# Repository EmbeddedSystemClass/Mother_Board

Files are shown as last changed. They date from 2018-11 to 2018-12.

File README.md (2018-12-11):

# ZJUNlict Mother Board Description
 
The mother board is used to convert between different logic levels (5V TTL <-> 3.3V TTL), improve signal quality and provide interface to the [motor driver board](https://github.com/ZJUNlict/Motor_Driver_Board), the [core board](https://github.com/ZJUNlict/Core_Board), the [nRF2401A](https://www.nordicsemi.com/eng/Products/2.4GHz-RF/nRF2401A) module, four [encoders](https://www.usdigital.com/) and a infrared sensor. (The board is designed using [Altium Designer](https://www.altium.com/altium-designer/) 17.1)

The 2D and 3D design views are shown below:

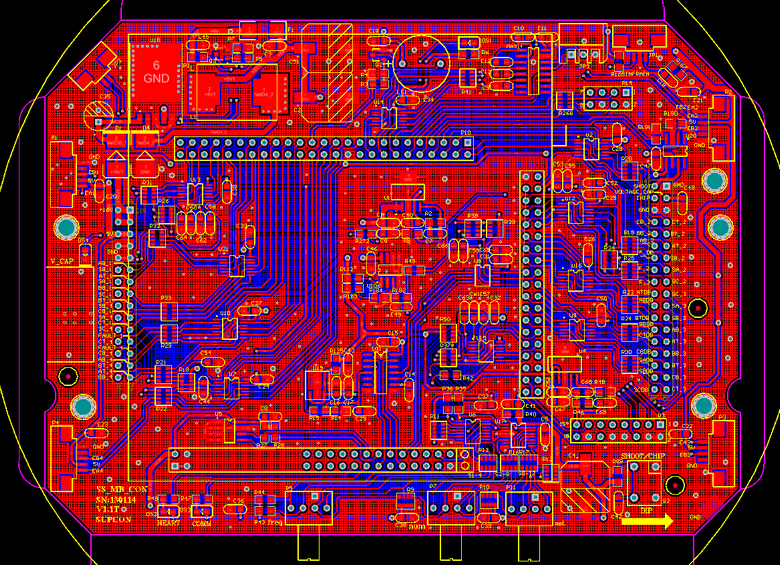
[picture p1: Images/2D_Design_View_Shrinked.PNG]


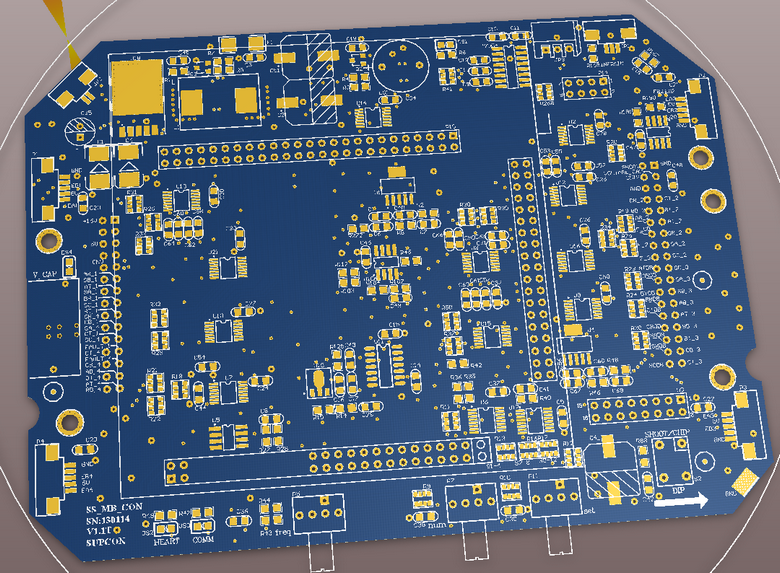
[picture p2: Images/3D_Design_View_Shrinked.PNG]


The main features are:

* Provide power supply (LM2576T-5.0 and TPS79401) for the core board and components on the mother board. (LiPo Battery (4S) 14.8-16.8V to 5V and 3.3V)
* Schmitt-trigger inverters (74LV14A, SN74HC14) complete the logic level convert and improve the signal quality.
* A/D (TLC0834) measures the battery and capacitor voltage.
* I/O expander (PCA9557PW) and rotary DIP switch (A6R/A6RV) for easier robot number, frequency and mode set.
* EEPROM (AT24C08) stores calibration data for each robot.
* Serial port (MAX232CSE) for communication with PC.

The photos of the mother board are shown below as references. 

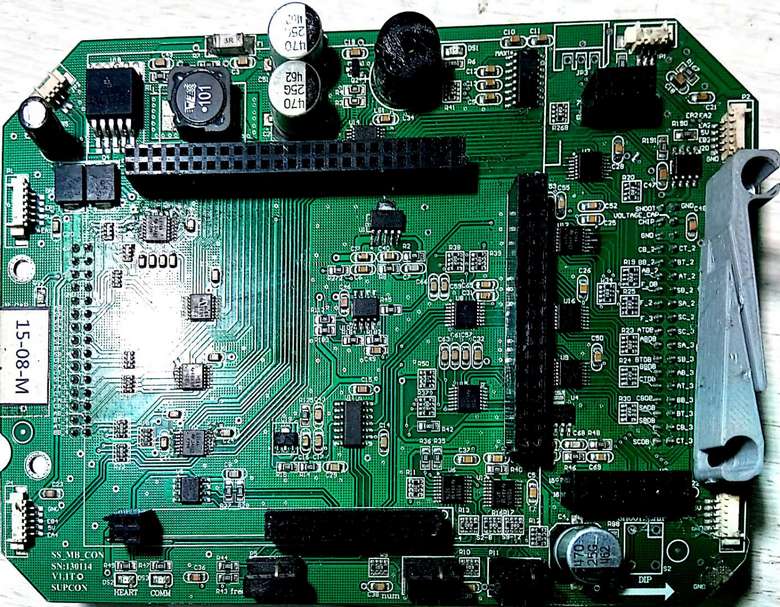
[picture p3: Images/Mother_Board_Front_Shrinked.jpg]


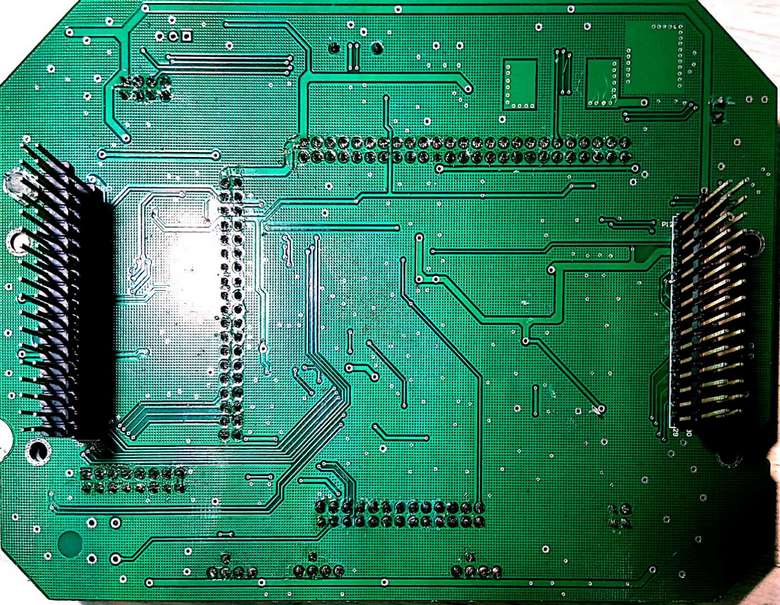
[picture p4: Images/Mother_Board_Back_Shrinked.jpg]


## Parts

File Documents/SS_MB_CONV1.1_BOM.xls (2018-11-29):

No. | Name | Code | Spec | Pos | Brand | Package | Quantity | Unit | Attribute | Notice
110021001 | IC | AT24C08B-SH |  | U5 | Atmel | SO-G8 | 1
110031001 | IC | LM393D |  | U106 |  | SOIC-8 | 1
110031003 | IC | 74HC14PW |  | U2, U9, U10, U16, U21 |  | TSSOP14 | 5
110031004 | IC | 74LVC14APW |  | U7, U8, U12, U13, U14, U15, |  | TSSOP14 | 6
110031005 | IC | PCA9557PW |  | U6, U17 |  | TSSOP16 | 2
110051001 | MAX232CSE(16) |  | +-15KV ESD-PROTECTED, +5V RS-232 TRANSCEIVERS | MAX1 |  | NSO16 | 1
110051004 | IC | TLC0834CD |  | U11 |  | SO-14 | 1
110051005 | IC | MC34152DG |  | U20 |  | SOIC-8 | 1
110061001 | IC | TPS79401/501 |  | U1, U4 |  | SOT223-6 | 2
110061002 | IC | LM2576D2T-005G |  | U18 |  | D2PAK | 1
111011001 | LED |  | 1.7V,0805,Green | DS1, DS2，DS3, DS4 |  | 0805D | 4
112011001 | Diode |  | SS36，60V,3A | D1, D4 |  | DO-214AB | 2
112021001 | Triode | 9014B |  | Q2, Q3 |  | SO-G3/Y1 | 2
112031001 | Voltage Reference | TL431ACPK |  | U19 | TI | SOT89 | 1
113021001 | Inductance | MSS1260T-100uH |  | L1 | Coilcraft | L | 1
115021001 | Resistance |  | 2.2K 1% | R3, R5 |  | 0805R | 2
115021002 | Resistance |  | 300 1% | R1 |  | 0805R | 1
115021003 | Resistance |  | 51k 1% | R2, R46 |  | 0805R | 2
115021005 | Resistance |  | 1.6K1% | R35, R36 |  | 0805R | 2
115021007 | Resistance |  | 100 1% | R167 |  | 0805R | 1
115021008 | Resistance |  | 10k 1% | R27, R28, R43, R44, R45, R88, R182, R183, R190, R191 |  | 0805R | 10
115021010 | Resistance |  | 1K 1% | R4, R7, R40, R112, R272 |  | 0805R | 5
115021013 | Resistance |  | 20K 1% | R168 |  | 0805R | 1
115021014 | Resistance |  | 22 1% | R42 |  | 0805R | 1
115021015 | Resistance |  | 22k1% | R15 |  | 0805R | 1
115021016 | Resistance |  | 2K 1% | R184 |  | 0805R | 1
115021017 | Resistance |  | 3.3k 1% | R14 |  | 0805R | 1
115011009 | Resistance |  | 30k 1% | R8, R48 |  | 0805R | 2
115021022 | Resistance |  | 470 1% | R125 |  | 0805R | 1
115021024 | Resistance |  | 510 1% | R6, R47, R49 |  | 0805R | 3
115051001 | Resisters Packs |  | 10K 1% | R9, R10, R12, R18, R26, R34, R39 |  | 0603 Resisters Packs | 7
115051002 | Resisters Packs |  | 2K 1% | R11,R50 |  | 0603 Resisters Packs | 2
115051003 | Resisters Packs |  | 22 1% | R13, R16, R17, R19, R20, R21, R22, R23, R24, R25, R29, R30, R31, R32, R33, R37, R38, R41, R268 |  | 0603 Resisters Packs | 19
115101001 | Fuse | 504-TR1/6125TD3-R | 3A 60V Slow Blow 2410 | F1 |  | 2512r | 1
116010002 | Electrolytic Capacitor | CAPPR2.5-6.3，6.3*11， | 100uf，25V,-55to+105℃ | C35 |  |  | 1
116011001 | Electrolytic Capacitor | J10 | 25V 470uf 10*10,-55to+105℃ | C2, C4, C51 | NICHICON |  | 3
116051001 | Ceramic Capacitor | 805 | 0.01uf,±10%，50V，-55to+125℃ | C44, C52, C53, C54, C55, C57, C58,C59, C60, C61, C62, C63, C64, C65, C66 |  |  | 15
116051002 | Ceramic Capacitor |  | 0.1uf,±10%，50V， -55to+125℃ | C3, C5, C6, C8, C14, C15, C17, C19, C20, C21, C22, C23, C24, C25, C26, C27, C28, C29, C30, C31, C32, C33, C34, C36, C37, C38, C39, C41, C42, C43, C45, C46, C47, C48, C49, C50, C67 |  | 805 | 37
116051005 | Ceramic Capacitor |  | 15pf,±10%，50V， -55to+125℃ | C7, C68 |  | 805 | 2
116051008 | Ceramic Capacitor |  | 1uf,±10%，50V， -55to+125℃ | C1, C9, C10, C11, C12, C13, C16, C56 |  | 805 | 8
116051009 | Ceramic Capacitor |  | 2.2uf,±10%，50V， -55to+125℃ | C40, C69 |  | 805 | 2
116051011 | Ceramic Capacitor |  | 4.7uf,±10%，50V， -55to+125℃ | C18 |  | 805 | 1
117020001 | Button | CTS-61R-V |  | S2 | CHAU-HUA |  | 1
117040001 | Rotary DIP Switch | A6RV-161RF |  | P5, P7, P11 | CHAU-HUA | A6RV-161RS | 3
118031001 | Connector | 1132R-SMT-3P |  | JP1 | SHPEAK | SMD-3P-1.25 | 1
118031002 | Connector | 1132R-SMT-2P |  | JP2 | SHPEAK | SMD-2P-1.25 | 1
118031003 | Connector | 1132R-SMT-5P |  | P1, P2, P3, P4 | SHPEAK | SMD-5P-1.25 | 4
118040001 | Connector | 201DLS-2*18PG-8.5/13.8/3.0 |  | P13 | SHPEAK | HDR2X18 | 1
118040002 | Connector | 203S-3C-2X4P-8.5/3.0 |  | P14 | SHPEAK | HDR2X4 | 1
118050004 | nRF2401A Connector | 203S-3C-2X8P-8.5/3.0 |  | U3 | SHPEAK | HDR2X8 | 1
118050002 | Connector | 203S-3C-2X25P-8.5/3.0 |  | 1 | SHPEAK |  | 1
118050022 | Connector | 203S-3C-2X19P-8.5/3.0 |  | 1 | SHPEAK |  | 1
118050036 | Connector | 203S-3C-2X13P-8.5/3.0 |  | 1 | SHPEAK |  | 1
118050037 | Connector | 203S-3C-2X2P-8.5/3.0 |  | 1 | SHPEAK |  | 1
118050006 | Connector | 201DLS-2*15PG-8.5/13.8/3.0 |  | P12 | SHPEAK | HDR2X15 | 1
119020001 | Buzzer | SD1209T5-A1 | 5V 60mA 12mm*9mm | LS1 | TDK | Buzzer | 1
133010001 | nRF Module | NRF2401A |  |  |  |  | 1
135010001 | Core Board | EP3C25 |  |  | ALTERA |  | 1

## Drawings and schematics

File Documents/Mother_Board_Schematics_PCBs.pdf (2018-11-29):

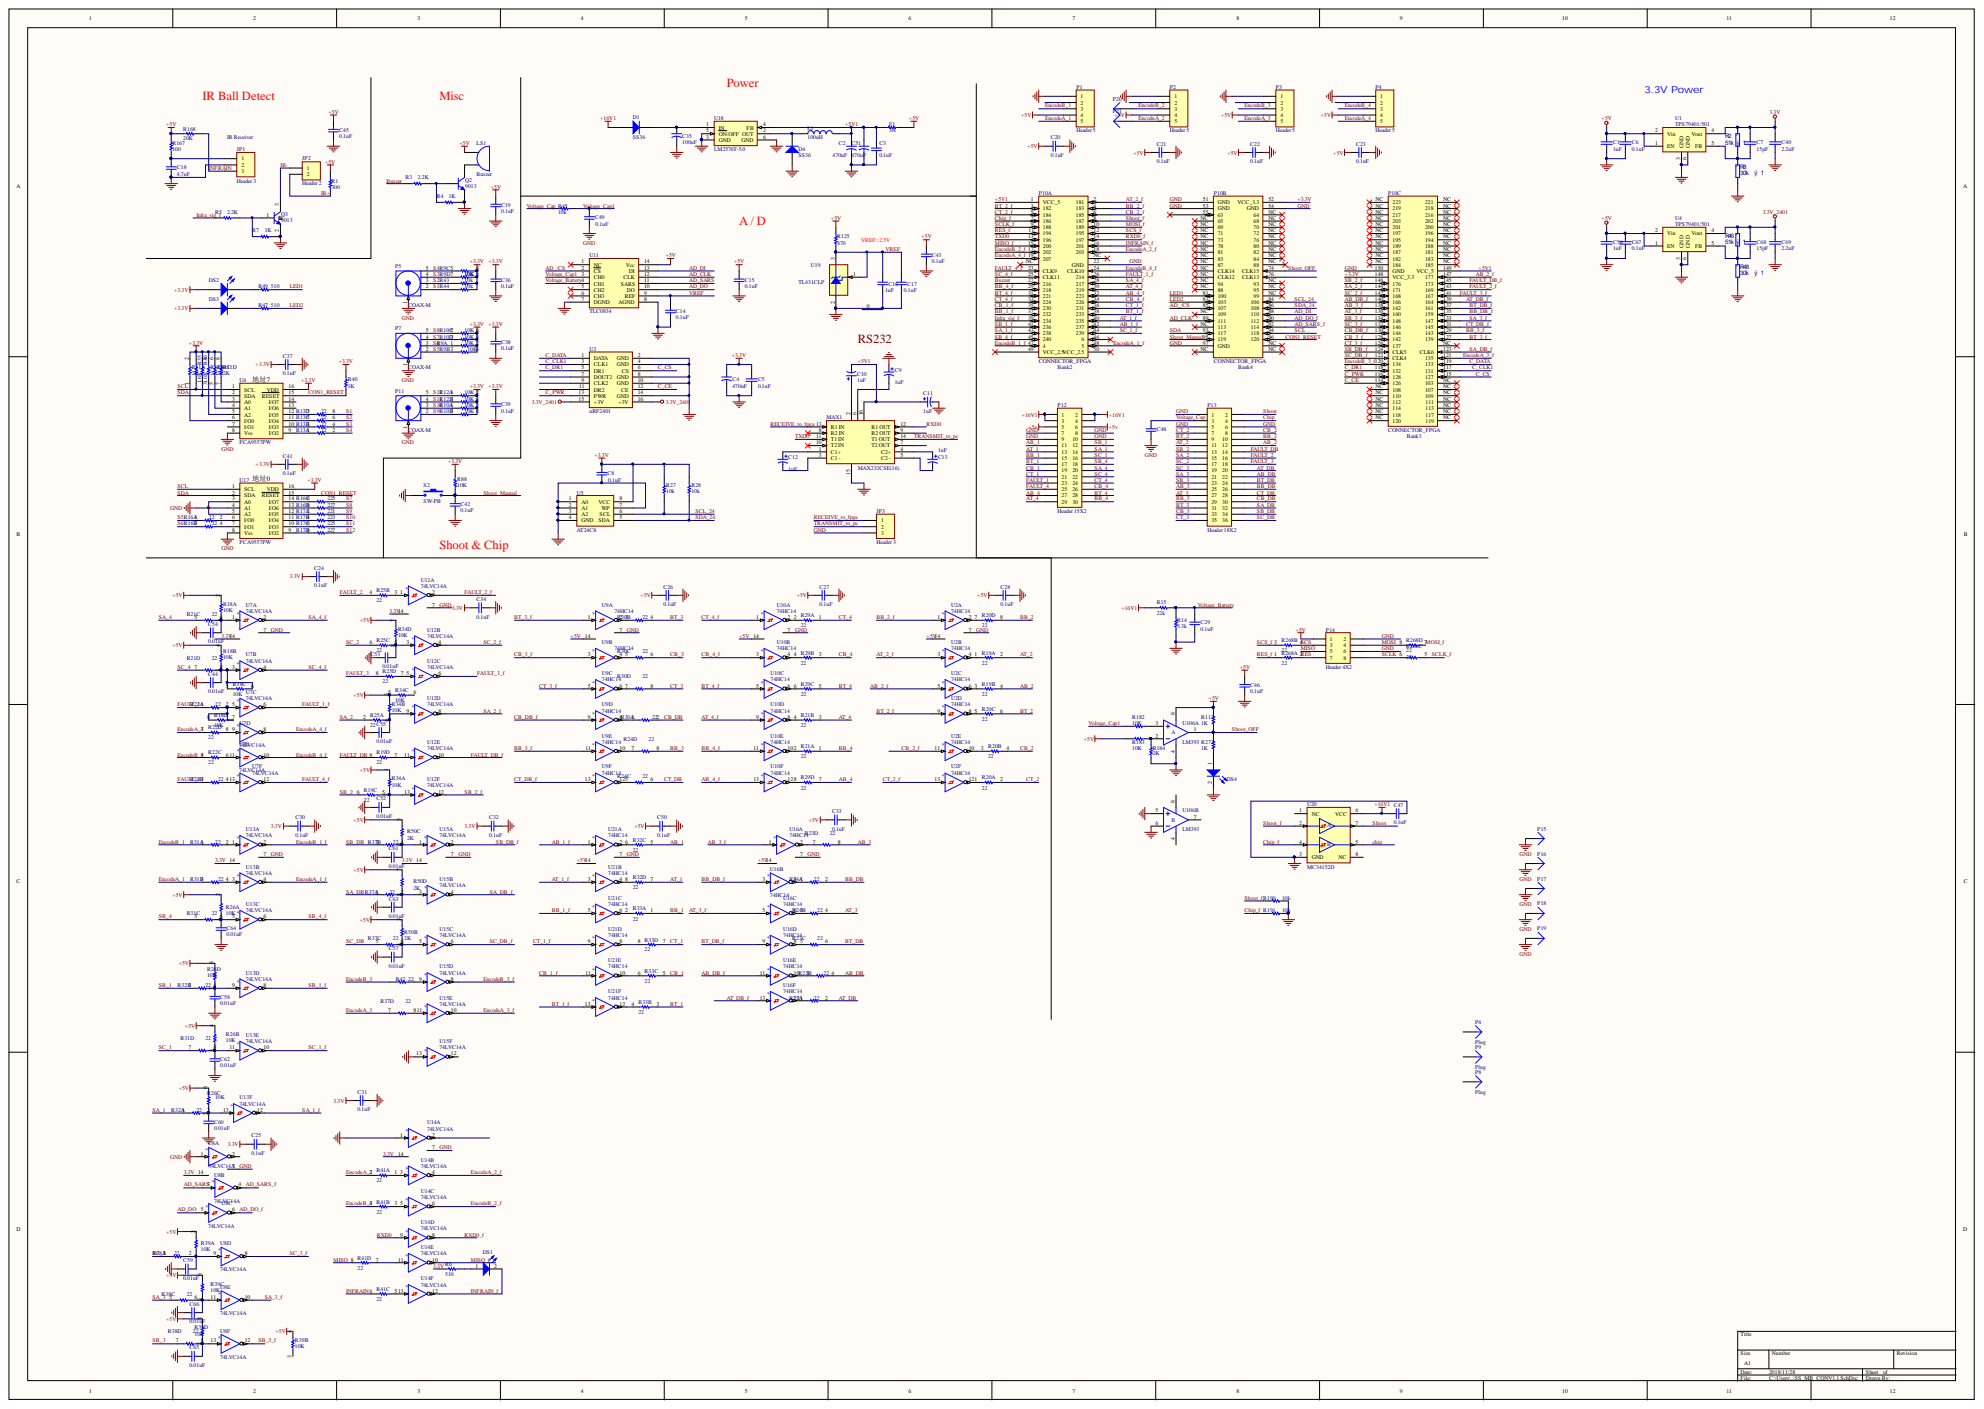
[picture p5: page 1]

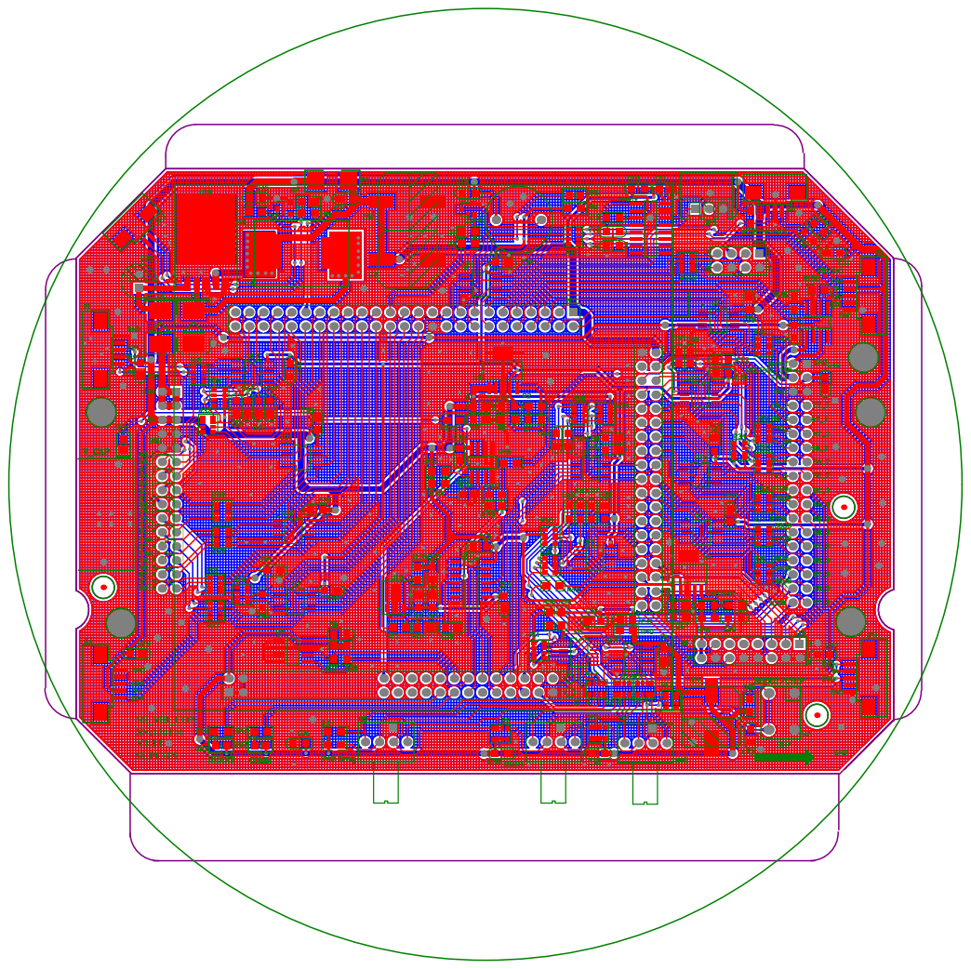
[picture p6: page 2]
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

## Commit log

2018-11-19 Add PCB files
    [SS_MB_CONV1.1.PcbDoc, SS_MB_CONV1.1.SchDoc, SS_MB_CONV1.1.xls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]
2018-11-29 Modify BOM List
    [SS_MB_CONV1.1.xls, SS_MB_CONV1.1_BOM.xls]
